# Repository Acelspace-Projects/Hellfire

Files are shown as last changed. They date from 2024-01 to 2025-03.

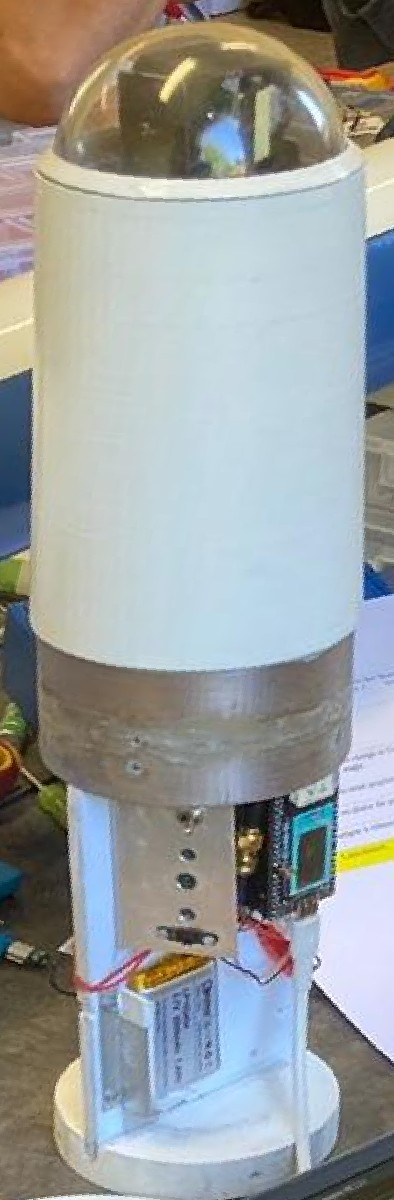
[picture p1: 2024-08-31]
Documentation/RapportDeProjet/img/IMG-20240712-WA0011~2.jpg

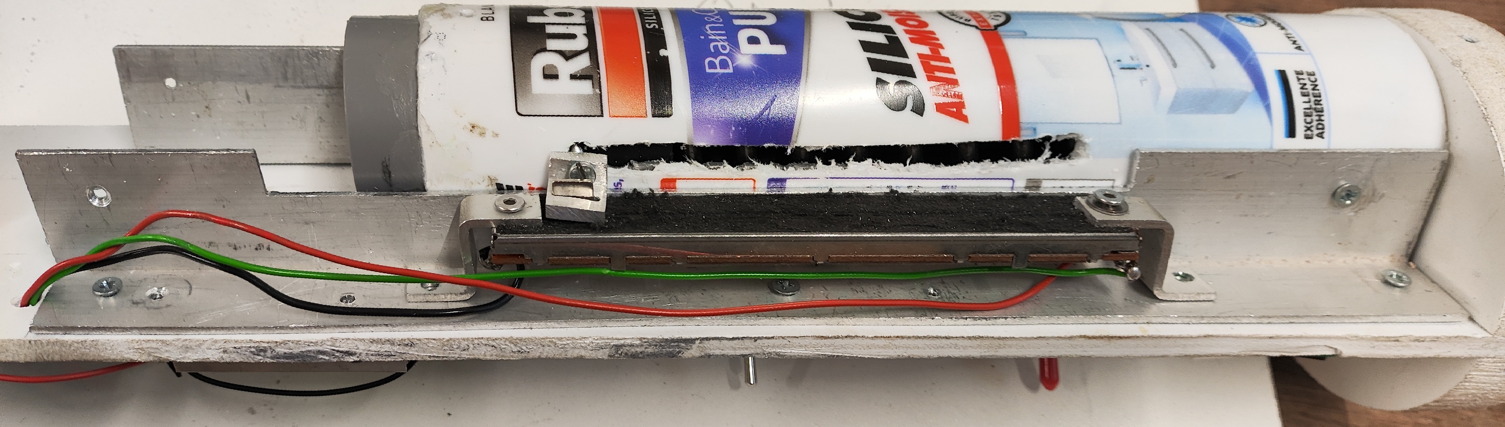
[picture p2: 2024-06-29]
Documentation/RapportDeProjet/img/IMG_20240511_170722~2.jpg

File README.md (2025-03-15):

<h1 align="center">
    <br>
    <a href="https://github.com/Acelspace-Projects/Hellfire">
        Acelspace logo
    </a>
    <br>
    <b>Hellfire</b>
</h3>

<h3 align="center">
    Ceci est un dépot pour le projet Hellfire utilisé pour le versionning et pour avoir des backups.
</h3>

<div class="badges" align="center">
    
    
</div>

---

### Description
Hellfire est un projet du club Acelspace.

### Liens
- [StabTraj](https://github.com/Acelspace-Projects/Hellfire/blob/main/Documentation/StabTraj/ST-(StabTraj)_Hellfire.xlsx)
- [Dossier de définition](https://github.com/Acelspace-Projects/Hellfire/blob/main/Documentation/DossierDeDefinition/DDD_Hellfire.pdf)
- [Dossier technique](https://github.com/Acelspace-Projects/Hellfire/blob/main/Documentation/DossierTechnique/DT_Hellfire.pdf)

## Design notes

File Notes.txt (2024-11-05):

# Matériel final:

## Meca:
* https://www.ressorts-sodemann.fr/13860 (ressort)

## Elec:
* https://heltec.org/project/wireless-tracker/ (telem + GPS)
* https://www.adafruit.com/product/960 (antenna)
* https://www.adafruit.com/product/851 (antenna adapter)
* https://www.adafruit.com/product/2796 (microcontrolleur)
* https://www.adafruit.com/product/4565 (lsm6dsox+lis3mdl sensor)
* https://www.adafruit.com/product/258 (x2 batteries)

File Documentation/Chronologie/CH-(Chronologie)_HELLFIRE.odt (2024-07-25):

Chronologie de Hellfire

H- | Action | Lieu | Matériel | Qui?
Toujours | Lire et porter la chronologie | -- | Chronologie | Dimitri
-- | Rassemblement du matériel | Zone travail club | Chronologie Tournevis+Clé allen Piles/Batteries chargées Jack Dispositif de télémesure Scotch+couteau Ordinateur | Tous
-- | Vérification minuterie principale: la trappe s'ouvre après 16s | Zone travail club | Tournevis | Clément
-- | Récupération matériel | Zone travail club | Voir liste | Tous
-- | Dévissage de l’ogive pour Changement des piles Formatage des cartes SD | Zone travail club | Tournevis, piles, scotch, ordinateur | Clément
2h | Repliage parachute | Zone travail club | Parachute | Tous
1h45 | Verrouillage de la trappe | Zone travail club | Mains | Clément
1h20 | Transport zone tente | Camion militaire | Voir Liste | Tous
45m | Transport zone rampe | Camion militaire | Voir Liste | Tous
42m | Activation de la station sol | Rampe de lancement | Ordinateur, Dispositif de télémesure | Dimitri
40m | Mettre la fusée en rampe | Rampe de lancement | Fusex | Tous
35m | Fixage du fil jack à la rampe Fixage du fil jack à la fusée | Rampe de lancement | Fil jack | Clément
32m | →Allumage du séquenceur principal: - Diode bleue allumée - Diode blanche allumée - Diode rouge allumée ⚠️ Aucune diode ne clignote !! →Activation de l’expérience du tensionomètre: Vérification diode verte allumé →Activation de la télémétrie: Demander autorisation émission 868.138 Mhz Allumage => diode blanche allumée Vérification de la connection à :la station sol La connection GPS est en initialisation →Activation de l'expérience IMU: Dernier interrupteur du panneau principal | Rampe de lancement | Tournevis | Clément
26m | Remettre les vitres de protection des panneaux de contrôle en place + SCOTCH | Rampe de lancement | Mains | Clément
25m | →Allumage caméra : - enlever le dôme, - allumer la caméra - remettre le dôme -> led allumée →Vérification de l'obtention des positions GPS | Rampe de lancement | Mains | Clément
10m | Faire monter la rampe et l'orienter dans le bon angle | Rampe de lancement | Manette de contrôle de la rampe | Gars du CNES
8m | Retour en zone pupitre (lancement) Retour en tente Jupiter (télem) | -- | -- | Clément Dimitri
6m | Mise en place du propulseur | Rampe de lancement | Propulseur | Pyro-techniciens
10s | Compte à rebours | Tente | Voix | Tous
- | Lancement | Pupitre de mise à feu | Mains | Clément

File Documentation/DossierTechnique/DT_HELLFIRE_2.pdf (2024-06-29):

Dossier Technique Hellfire – Hellfire FX10 – 2024-06-09

# DOSSIER TECHNIQUE HELLFIRE

2024

# FAJAL Dimitri CHAUVIN Geoffroy LORIN DE LA GRANDMAISON Clément LORIN DE LA GRANDMAISON Alexandre

Hellfire FX10 – 1/7

# SOMMAIRE

## I. Plan général _________________________ Page 3 II. Conception mécanique ________________ Page 4

1) Informations générales | Page 4
2) Montage ailerons | Page 4
3) Système de retenue du propulseur | Page 4

## III. Système d’éjection _________________ Page 5

1) Plan mécanique | Page 5
2) Plan électrique (séquenceur) | Page 5

## IV. Expériences (TensionomèTRE TRAJECTOGRAPHIE caméra) _________________________________ Page 6

1) Tensionomètre | Page 6
2) TRAJECTOGRAPHIE | Page 7
3) Caméra | Page 7

# I. PLAN GÉNÉRAL

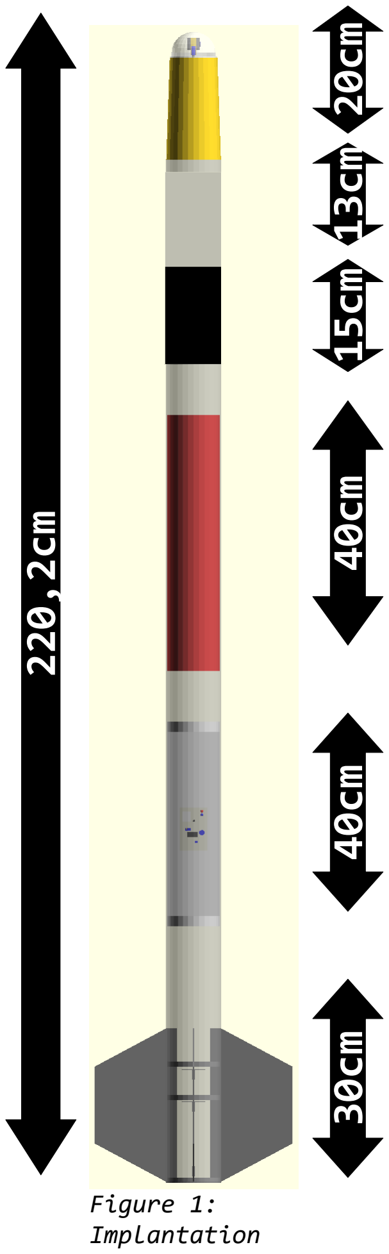
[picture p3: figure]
Xmm; Figure 1: Implantation

→ Ogive dôme sur un rétreint, servomoteur et caméra rotative (180) soutenue par un ventilateur

→ Support secondaire : Télémétrie LoRa et prise de mesures d’accélération et de rotation

→ Centrale inertielle

→ Trappe d’éjection du parachute

→ Support principal contenant l’expérience secondaire de mesure de la tension aux sangles du parachute (tensionomètre), le séquenceur principal et le panneau de contrôle

→ Montage des ailerons et système de retenue du propulseur

Nous utilisons un total de 5 piles 9V : trois dans la minuterie secondaire et deux dans la minuterie principale.

# II. CONCEPTION MÉCANIQUE

# 1) INFORMATIONS GÉNÉRALES

La peau porteuse est un tube en aluminium de 2mm d’épaisseur, de 100mm de diamètre et de 2m de long. Elle offre une grand solidité. L’ensemble des montages à l’intérieur sont solidement
accroché au tube par des vis.

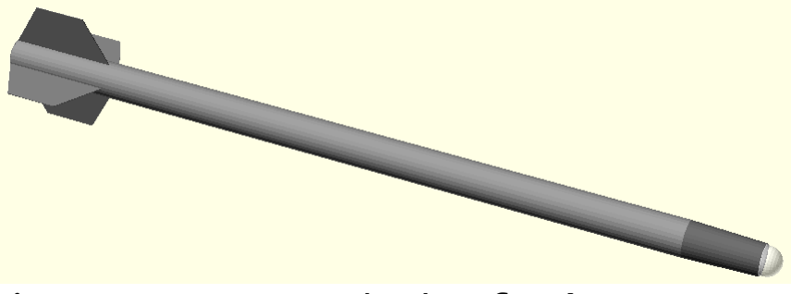
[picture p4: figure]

L’ogive est formée de deux parties : un rétreint réduisant le diamètre à 80mm et un dôme de plastique sur le dessus (ce montage permet l’installation d’une caméra). Le tout mesure 19,5 cm en hauteur.

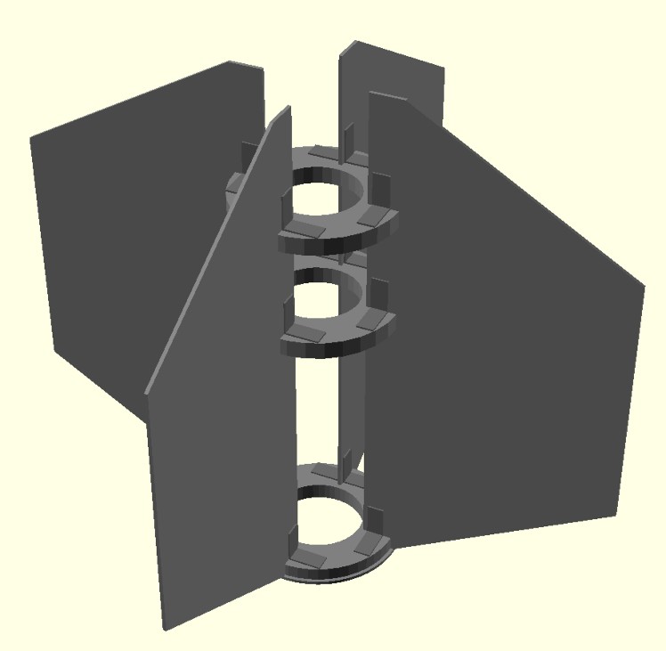
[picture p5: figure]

# 2) MONTAGE AILERONS

Les ailerons sont attachés à trois bagues en aluminium à l’aide d’équerres de métal.
Le montage complet est accroché au tube par avec des vis. La bague la plus inférieure est la plaque de poussée.
Elle transfère la poussée du propulseur au corps de la
fusée.

# 3) SYSTÈME DE RETENUE DU PROPULSEUR

Le propulseur est retenu par un petit montage en métal
accroché à la plaque de poussée.
Celui-ci est construit à l’aide d’un « Sandwich » de pièces en aluminiums usinées.
Pour monter le propulseur, il suffit de l’insérer dans le corps de la fusée. Lorsqu’il est bien montée, un petit « clic » est audible lorsque la pêne ressort du montage.
Pour enlever le propulseur, il faut pousser la poignée avec le doigt. Étant accroché à la pêne il relâchera le propulseur qui peut alors être retiré.

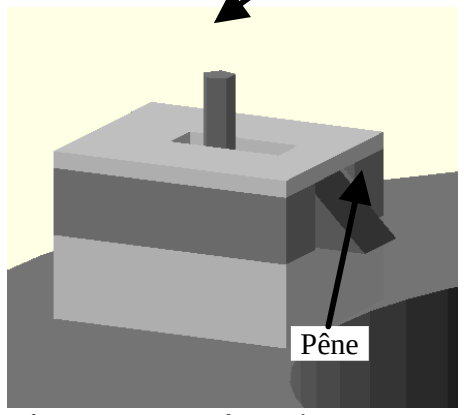
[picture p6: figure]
Pêne

Figure 4: Sytème de retenue du propulseur

Poignée

Figure 3: Montage des
ailerons

Figure 2: Corps de la fusée

# III. SYSTÈME D’ÉJECTION

# 1) PLAN MÉCANIQUE

Le système de récupération est un parachute de ballon sonde circulaire éjecté latéralement de la fusée. Pour cela, il est attaché à la trappe qui l’emporte lors de son ouverture. Afin de s’assurer de l’ouverture de la

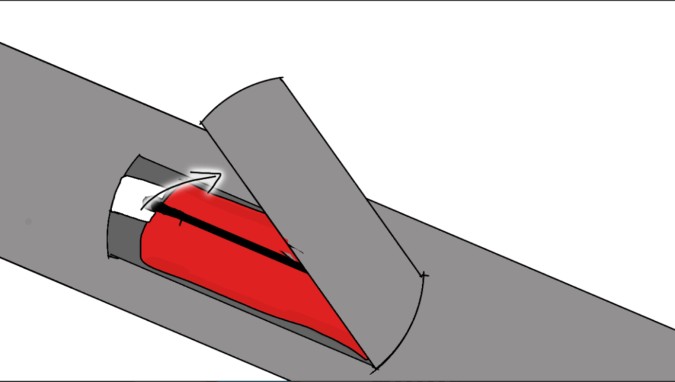
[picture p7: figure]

trappe, elle est poussée par une lame d’essuie-glace à la manière d’un ressort.

# 2) PLAN ÉLECTRIQUE (SÉQUENCEUR)

Une minuterie analogique soudée par nos soins permet le décompte de l’ouverture de la trappe. Un peu avant

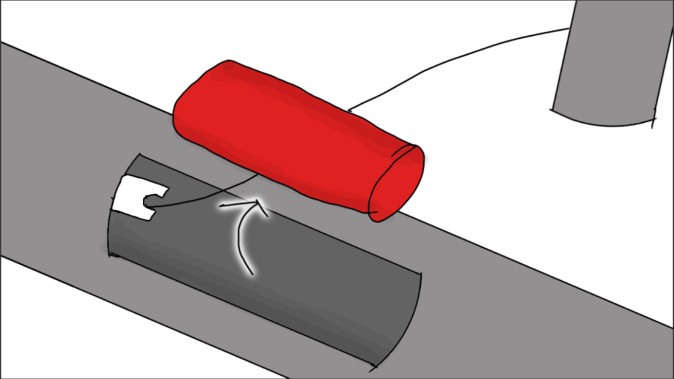
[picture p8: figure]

l’apogée, le séquenceur enclenche un moteur. Sur celui-ci est accroché une cloche qui en tournant libère la trappe.

Figure 5: Ejection de la
trappe

Figure 6: Sortie du
parachute

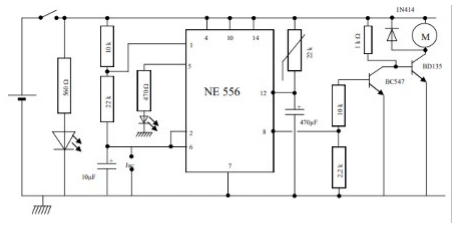
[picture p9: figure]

Figure 7: Schéma électronique du

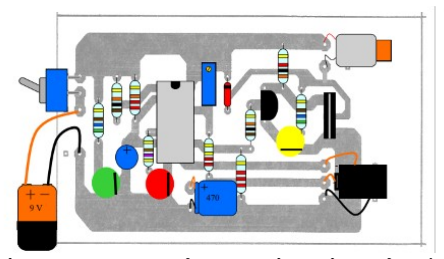
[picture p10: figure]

séquenceur | Figure 8: Représentation imagée du séquenceur

# IV. EXPÉRIENCES (TENSIONOMÈTRE TRAJECTOGRAPHIE CAMÉRA)

# 1) TENSIONOMÈTRE

La tension sera mesurée sur les sangles du parachute. Deux ressorts de 15cm chacun sont compressés par de la sortie du parachute. Ainsi le potentiomètre linéaire relié à un Arduino permettent d’effectuer l’acquisition des données qui sont sauvegardées en temps réel sur carte microSD.

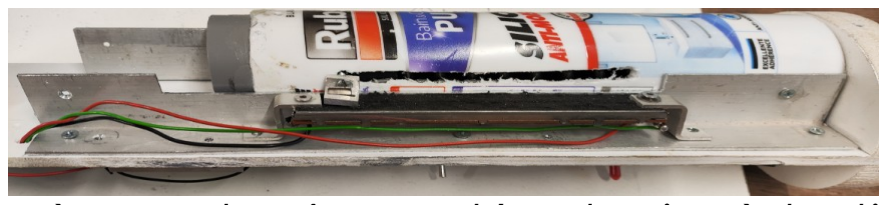
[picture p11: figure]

Après vol, les données sont récupérées et passées au travers d’une fonction de conversion qui transforme les données brutes (de 0 à 1023 données par la carte arduino) en donées exploitables (force exercée en kg).
Cette fonction de conversion est déterminée en appliquant des masses connues (poids d’altère et autres) au système entièrement assemblé. Une courbe d’étalonnage est alors établie sur un tableur pour ensuite faire apparaître la courbe de tendance dont l’équation est la fonction de conversion.

Figure 9: Le système est le même que l'an dernier à la différence qu'il sera maintenant composé de deux ressorts pour une plus grande résistance (1000 N) et qu'il n'est plus aligné avec la sangle (il faut maintenant une poulie dans la trappe)

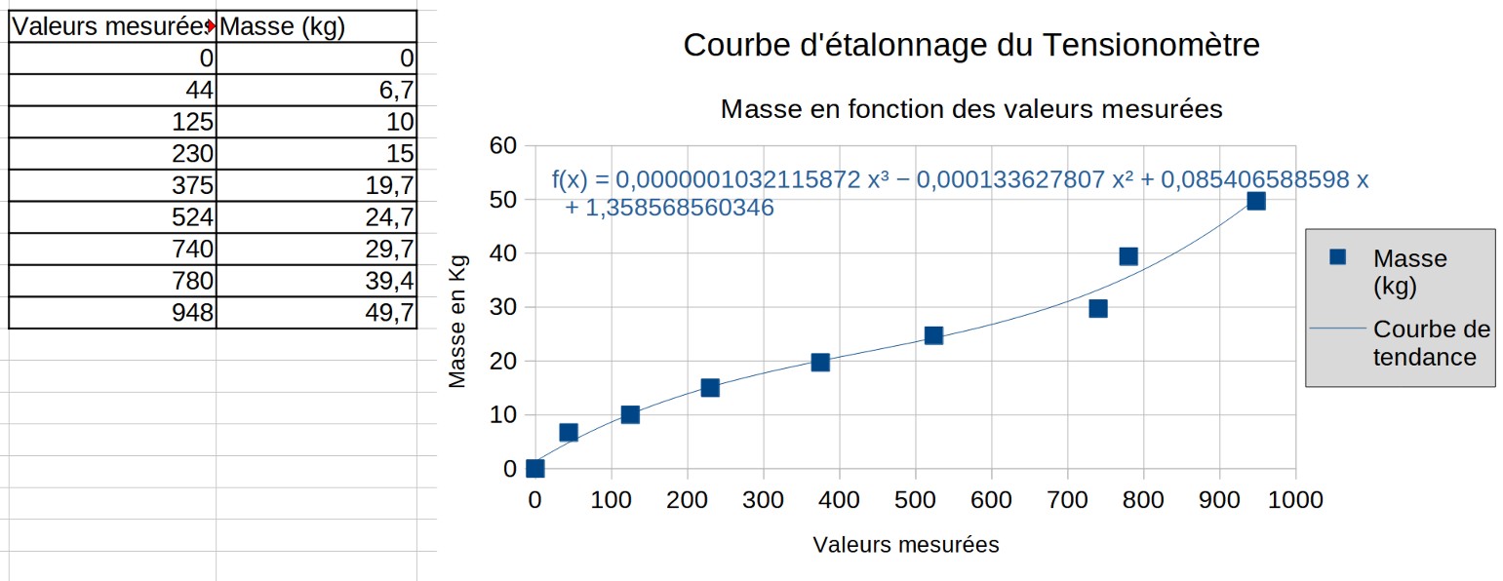
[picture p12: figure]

Figure 10: Courbe d'étalonnage du tensionomètre

# 2) TRAJECTOGRAPHIE

La trajectographie est assurée par de multiples IMUs, capteurs d’accélération et gyroscopes. Ceux que nous utilisons sont les LSM6DSOX (16g) et un LSM6DSO32 (32g). Ces capteurs permettrons d’effectuer post-vol une trajectographie. Un filtre de Kalman sera utilisé.
Le vol a en fait été simulé au préalable par un programme python nous donnant une idée générale du vol de la fusée. Les données accumulées en vol seront retransmises par télémétrie LoRa à l’équipe au sol en temps réel et les données GPS nous permettront de voir la position de la fusée.

# 3) CAMÉRA

Une caméra cubique, de 3.1 cm de côté, se trouve au sommet de la fusée, protégée par un dôme de plexiglas. Les images seront enregistrées sur une carte microSD et pourront être récupérées après le vol. Un système de servomoteur, faisant des allers-retours entre 0° et 180°, permet de l’orienter.
Ayant remarqué une perte de performance de la caméra lorsqu’elle surchauffait, nous avons décidé d’installer un ventilateur dans le dôme.

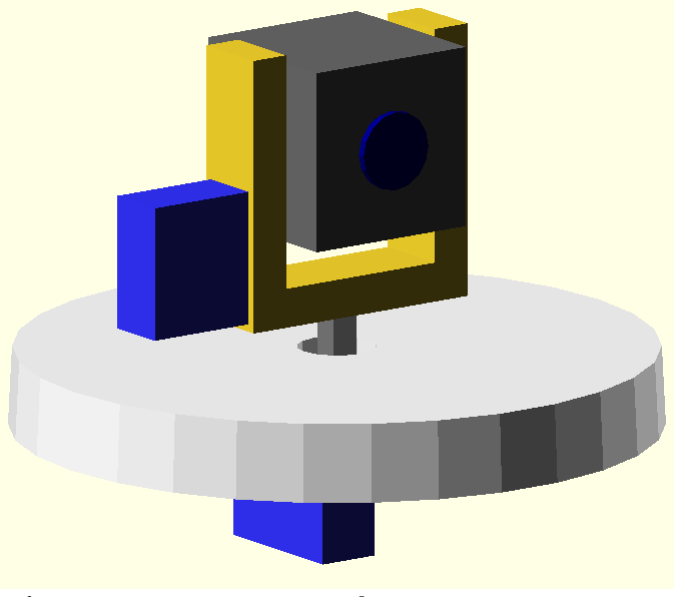
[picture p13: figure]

Figure 11: La caméra

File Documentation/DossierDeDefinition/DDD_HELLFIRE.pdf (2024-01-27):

Dossier de définition – Hellfire – 2023-2024

# DOSSIER DE DÉFINITION HELLFIRE

2023-2024

# BENAY Clément CHAUVIN Geoffroy FAJAL Dimitri KAE-NUNE Damien LORIN DE LA GRANDMAISON Alexandre LORIN DE LA GRANDMAISON Clément PINGLIER Etienne

Hellfire – 1/12

# SOMMAIRE

## Présentation de l’équipe ________________ Page 3

Présentation générale | Page 3
Les membres de l’équipe | Page 3

## Présentation de KARLAVAGNEN _____________ Page 5 Présentation d’HELLFIRE _________________ Page 6

Objectifs | Page 6
Reprise du corps de KARLAVAGNEN | Page 6

## Expériences _____________________________ Page 9

Mesures de la tension exercée sur les sangles du parachute «le
tensionomètre» | Page 9
Caméra montée sur axe rotatif + ventilateur | Page 10
Mesures de la vitesse (Pitot, Venturi et accéléromètre) | Page 11
Mesures de l’altitude et de la température | Page 12

# PRÉSENTATION DE L’ÉQUIPE

# PRÉSENTATION GÉNÉRALE

Notre groupe est constitué de 6 étudiants aux études variées (médecine, commerce, prépas) et d’un lycéen (lycée Sonia Delaunay à Villepreux). C’est cette diversité qui crée la richesse d’innovation de nos projets. Nous avons déjà mené plusieurs projets auparavant dont 2 projet Fusex ensemble : OGMA et KARLAVAGNEN. Chaque membre a mené à bien plusieurs projets et a donc de l’expérience en terme de conception, d’électronique, de mécanique ou même en programmation. Nous sommes encadrés par Roger POISSON, vétéran du C’SPACE et habitué des projets fusées et Sylvain BEAU, ingénieur en aérospatiale dans les systèmes embarqués.

# LES MEMBRES DE L’ÉQUIPE

Geoffroy CHAUVIN : étudiant à l’ESTACA. 7 projets à son actif dont 2 projets Fusex, OGMA et KARLAVAGNEN.

### Clément LORIN DE LA GRANDMAISON : élève de Première au lycée Sonia

Delaunay à Villepreux. 5 projets à son actif dont un projet Fusex, KARLAVAGNEN. Clément BENAY : étudiant en BTS maintenance des véhicules. 5 projets à son actif dont 2 projets Fusex, OGMA et KARLAVAGNEN.
Damien KAE-NUNE : étudiant en mathématiques, informatique, option éco finance à CYTECH. 5 projets à son actif dont 2 projets Fusex, OGMA et KARLAVAGNEN.
Etienne PINGLIER : étudiant à l’INSA de Rouen. 5 projets à son actif dont 2 projets Fusex, OGMA et KARLAVAGNEN.

### Alexandre LORIN DE LA GRANDMAISON : étudiant en médecine à la

Sorbonne. 5 projets à son actif dont 2 projets Fusex, OGMA et KARLAVAGNEN.

Dimitri FAJAL : étudiant en CPGE MPSI au lycée Jeanne d’Albret. 5 projets à son actif dont 2 projets Fusex, OGMA et KARLAVAGNEN. Chef de projet de la Fusex KARLAVAGNEN l’an passé.
Le chef de projet pour le projet de cette année est Alexandre LORIN DE LA GRANDMAISON.
Illustration | 1 | : Fusex KARLAVAGNEN en rampe

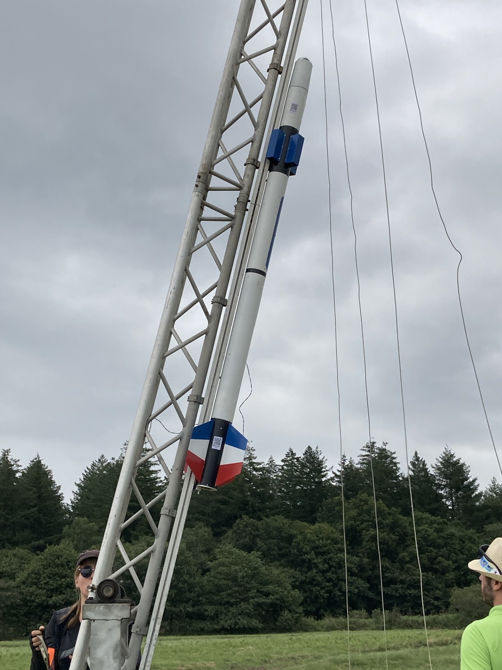
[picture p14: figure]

# PRÉSENTATION DE KARLAVAGNEN

KARLAVAGNEN est le projet que nous avons mis en œuvre durant la campagne de lancement 2022-2023 et qui a abouti à un vol nominal.
Le but du projet était de mesurer la tension aux sangles du parachute via notre tensionomètre maison. Nous mesurions aussi la vitesse de deux manières différentes, par tube de Pitot et par effet Venturi. Pour cela nous avions mis en place 4 blocs de PLA (deux qui contenaient nos capteurs et deux factices pour équilibrer) qui faisaient office d’ailerons : la Fusex possédait donc un bi-empennage pour le moins spécial. A cela s’ajoutait des mesures d’altitude via un BMP 180 et une ogive dôme qui abritait notre caméra montée sur servomoteur et refroidie par un ventilateur dont l’objectif était de filmer l’entièreté du vol. Enfin, notre Fusex embarquait à son bord une carte CATS qui nous fournissait des données en temps réel (position GPS, vitesse, altitude) via de la télémesure (système LoRa, 2,4GHz). Cette carte nous avait été prêté par l’école d’ingénieur Air Esia. Notre Fusex servait de test pour calibrer cette carte afin que nous fassions remonter, post-vol, à Air Esia les différents problèmes que nous aurions pu rencontrer avec la carte. En effet, Air Esia compte utiliser cette carte comme système de backup dans leur Fusex lors du concours européen EuRoc. Ce fut un excellent partenariat qui s’est soldé par une réussite puisque la carte a très bien fonctionné même si nous avons dû leur faire remonter quelques petits problèmes auxquels ils devront faire attention. Fort heureusement, ces problèmes se résolvent par un meilleur réglage de la carte.
Illustration | 2 | : L’équipe Fusex KARLAVAGNEN au complet

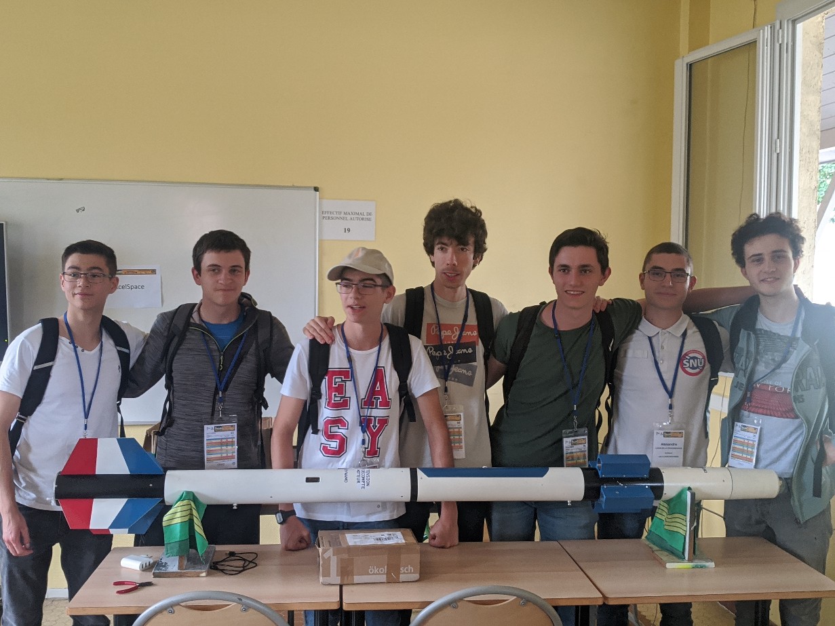
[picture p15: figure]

# PRÉSENTATION D’HELLFIRE

# OBJECTIFS

HELLFIRE est le nouveau projet Fusex que nous allons mettre en œuvre cette année. Il s’agit d’un projet spécial. En effet, nous allons réutiliser le corps de notre ancienne Fusex KARLAVAGNEN qui est intacte suite à un vol nominal. Les objectifs seront les mêmes que ceux de KARLAVAGNEN, à savoir :

- la mesure de la tension aux sangles du parachute via notre tensionomètre maison que nous comptons améliorer.
- la mesure de la vitesse de la Fusex par effet Venturi et par tube de Pitot grâce à quatre blocs de PLA qui contiennent nos capteurs et font office d’ailerons du haut, procurant à la Fusex un bi-empennage d’exception. Cependant, cette année, nous rajoutons un accéléromètre pour avoir encore plus de valeurs à comparer et pouvoir décider lequel des deux systèmes (Pitot ou Venturi) est le plus précis.
- la mesure de l’altitude à laquelle nous rajoutons cette année une mesure de la température grâce un BMP 180.
- filmer le vol grâce à une caméra positionnée dans notre ogive dôme, sur un servomoteur, lui permettant d’avoir une vision 180°. Elle est refroidie par un ventilateur.

# REPRISE DU CORPS DE KARLAVAGNEN

Pour la 1ère fois de l’histoire de notre club, nous comptons relancer une fusex ayant déjà volé. Ce sera donc le corps de Karlavagnen qui va reprendre sa route vers le ciel sous le nom d’Hellfire. Cela est possible pour plusieurs raisons :

- grâce à un vol nominal et une descente sans encombre, Karlavagnen nous est revenue en parfait état. On pourrait même croire qu’elle n’a pas encore volé…
- plusieurs expériences n’ayant pas fonctionné de manière optimale, il serait intéressant pour nous de les améliorer afin que cette fois-ci nous obtenions toutes les données voulues (Tensionomètre et effet Venturi) ;
- la majorité de l’équipe de Karlavagnen étant maintenant en études supérieures, nous ne pouvons que consacrer peu de temps à la réalisation d’une fusex. Avoir toute la mécanique déjà faite nous permet de nous centrer sur ce qui est important, à savoir, les expériences.

Ainsi, l’extérieur sera le même, c’est l’intérieur qui va se faire une peau neuve : toute l’électronique sera vérifié et refaite dans la majorité des cas par précaution. Les expériences seront similaires à celles de Karlavagnen mais seront toutes modifiées de façon à fonctionner de manière optimale. De plus, plusieurs capteurs seront rajoutées. De même, la peinture aura le droit à un petit retouchage.

Illustration | 3 | : Karlavagnen avant le vol | Illustration | 4 | : Karlavagnen après le vol

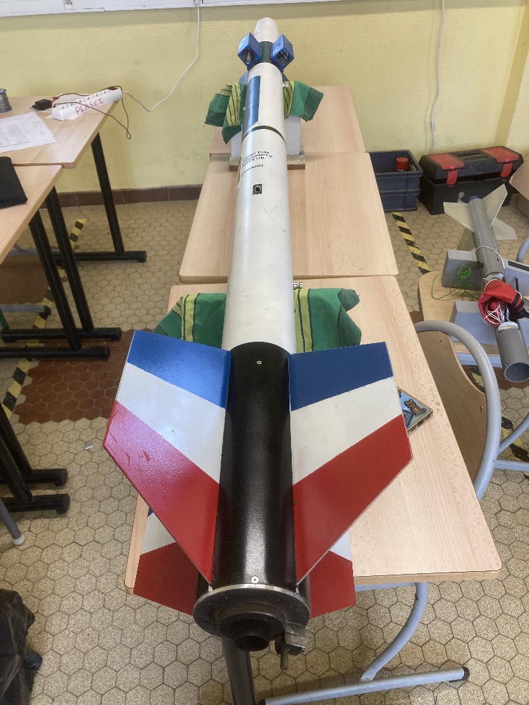
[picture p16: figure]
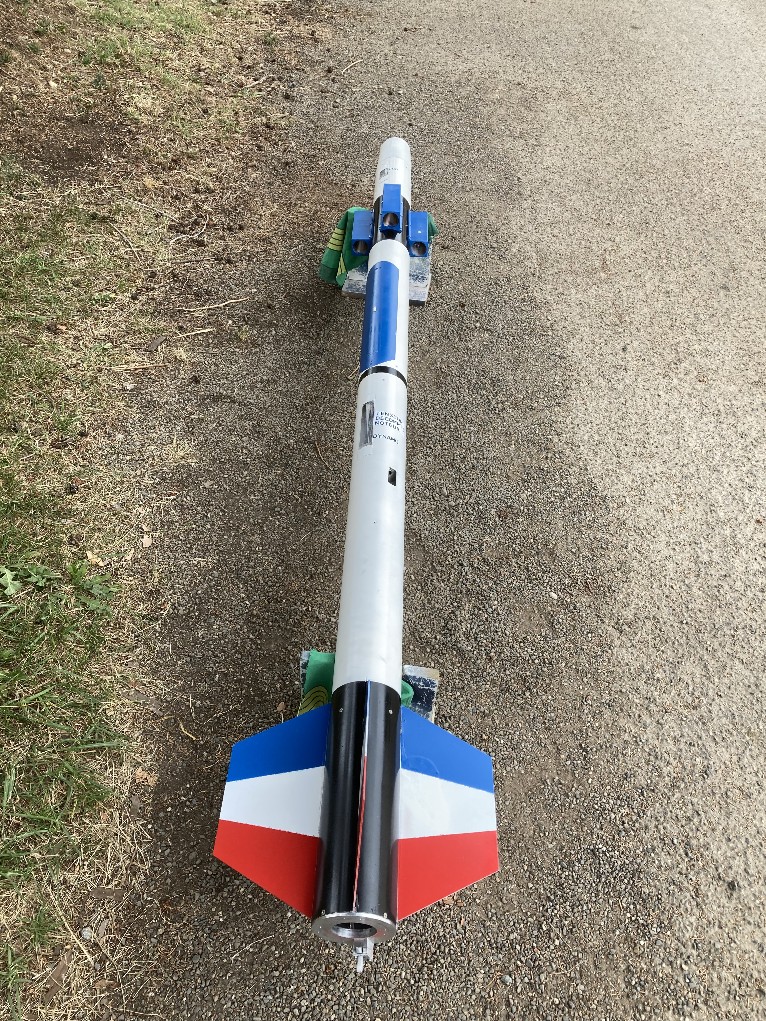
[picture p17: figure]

| | | | | De petites imperfections sont visibles sur la peinture suite au vol mais c’est tout, la mécanique, elle, dans son entièreté, est intacte.

Illustration | 5 | : CAO d’Hellfire

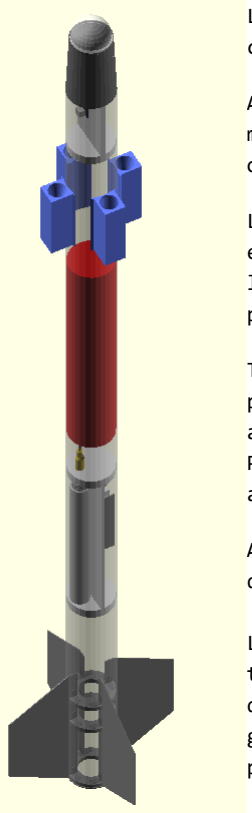
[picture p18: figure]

La partie mécanique d’Hellfire sera donc similaire à celle de Karlavagnen.

Actuellement, nous avons vérifié et testé toute la mécanique ayant volé (ailerons, tube, blocs de PLA, ogive) à la recherche d’éventuelles défaillances.

La seule partie mécanique présentant un léger défaut est un des quatre ailerons qui présente une très
légère | torsion | d’environ | 2° | à | son | extrémité,
probablement due à l’atterrissage. Cela sera corrigé.

Tout le reste est intacte, que ce soit : la bague de poussée, les bagues de centrage propulseur, les 3 autres ailerons, l’ogive, le dôme, les 4 blocs en PLA, la trappe et bien sûr la peau porteuse en aluminium.

Aucune déformation du tube d’aluminium n’a été détectée.

Le principal avantage que nous procure l’usage d’un tube d’aluminium est la grande résistance de ce dernier envers les chocs. C’est d’ailleurs une des garanties nous poussant à relancer cette peau porteuse sans risque.

# EXPÉRIENCES

# MESURES DE LA TENSION EXERCÉE SUR LES SANGLES DU PARACHUTE «LE TENSIONOMÈTRE»

Malheureusement, lors du vol de Karlavagnen, nous sommes à nouveau arrivés en buté du ressort. Cette année, nous comptons refaire entièrement la partie mécanique de cette expérience, en changeant notamment le ressort, pour la faire fonctionner correctement.

La tension sera mesurée sur les sangles du parachute. Toutefois, lors de l’ouverture du parachute, les sangles de ce dernier ne seront pas directement alignées avec le potentiomètre. Elles passeront dans une poulie fixée à l’intérieur de la fusée afin de rediriger l’effort directement sur le potentiomètre. Sans cette poulie, le parachute arracherait le système et la fusée n’aurait alors plus de système de récupération.

Le potentiomètre linéaire sera relié à un Arduino permettant d’effectuer l’acquisition des données qui seront sauvegardées en temps réel sur carte MicroSD.

Le nouveau ressort aura donc une capacité de compression strictement supérieure à 1000N pour nous éviter tout désagrément et nous permettre d’avoir une plage de mesure complète.

Il sera protégé par un tube en PVC qui lui permettra de se compresser de manière linéaire sans déviation. Le tube en PVC sera lui-même immobilisé par deux équerres métalliques présentes de chaque côté. Une encoche présente dans la longueur du tube permettra le raccordement du capteur au ressort. Le capteur pourra donc suivre l’entière compression du ressort pour des mesures les plus précises possibles.

Illustration | 6 | : Le tensionomètre maison qui sera refait en terme de mécanique

# CAMÉRA MONTÉE SUR AXE ROTATIF + VENTILATEUR

Une caméra cubique, de 3.1 cm de côté, se

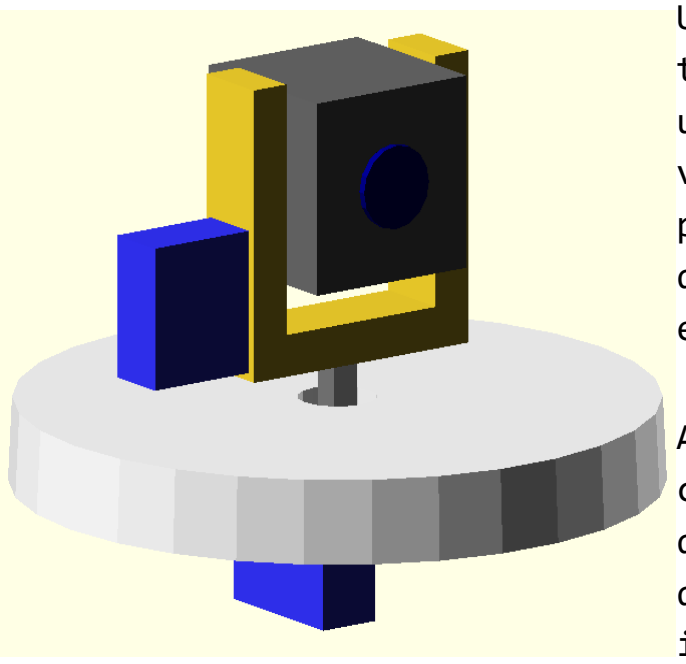
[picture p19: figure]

trouvera au sommet de la fusée, protégée par un dôme de plexiglas. Une vidéo complète du vol sera enregistrée sur une carte MicroSD et pourra être récupérée après le vol. Un système de servomoteur, faisant des allers-retours entre 0° et 180°, permettra de l’orienter.

Ayant remarqué une perte de performance de la caméra lorsqu’elle surchauffait, nous avons décidé d’installer sous elle un ventilateur dans le dôme afin d’éviter d’avoir une vidéo inexploitable.

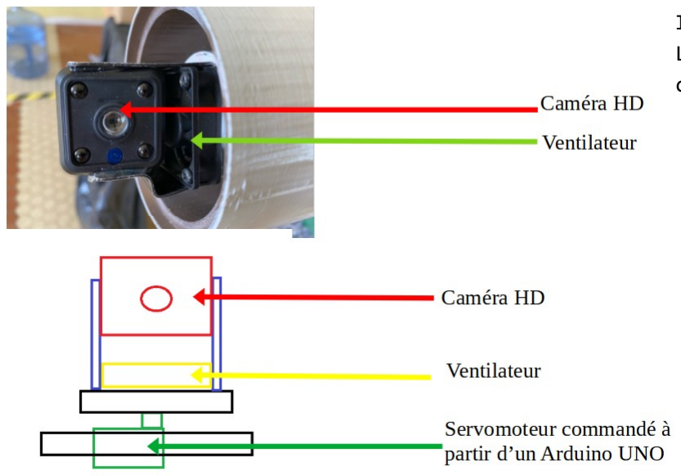
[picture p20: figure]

Illustration | 8 | :
L’ensemble du système
caméra mis en place

Si nous jugeons la qualité de la caméra trop faible quant à la résolution vidéo et au framerate, il se peut que nous la changions.

Illustration | 7 | : La caméra

# MESURES DE LA VITESSE (PITOT, VENTURI ET ACCÉLÉROMÈTRE)

La mesure de la vitesse sur notre fusée va

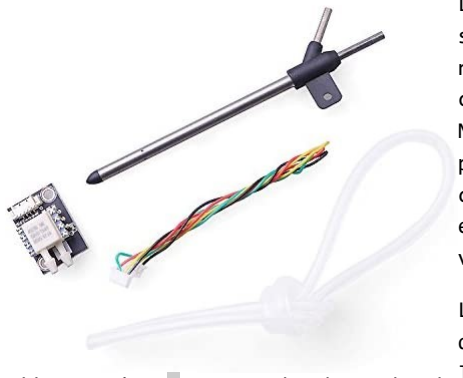
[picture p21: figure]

s’effectuer de deux manières. Tout d’abord nous utiliserons un tube de Pitot (ci-contre) pour réaliser une première mesure. Nous utiliserons ensuite un effet Venturi pour réaliser une seconde mesure que nous comparerons à la première afin d’avoir une estimation beaucoup plus précise de la vitesse de la fusée.

Les données seront récupérées à l’aide de quatre parallélépipèdes en PLA placés sur le haut de la fusée, alignés avec les ailerons dans son axe. Ce système sera le même que celui de notre ancienne Fusex KARLAVAGNEN : deux des 4 blocs en PLA contiendront les tubes de mesure de vitesse, qui achemineront l’air jusqu’au MPX5010DP, capteur différentiel de pression placé sur la carte Arduino.

Ainsi, l’un des blocs contiendra un tube de Pitot et un autre nous permettra d’utiliser l’effet Venturi avec un rétrécissement du diamètre intérieur. Les deux autres seront factices, afin d’éviter de perturber la stabilité.

Illustration | 9 | : Exemple de tube de
Pitot (à titre illustratif)

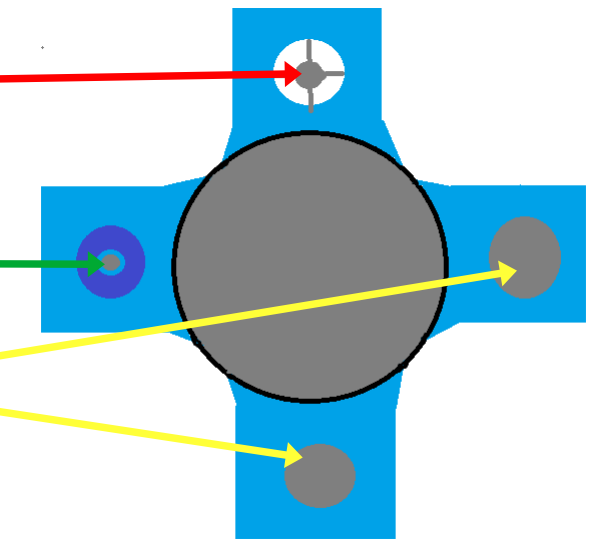
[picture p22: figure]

Tube de pitot

Tube Venturi

Illustration | 10 | : Positionnement des
différentes expériences (Venturi et Pitot)

Tubes factices qui
permettent
d’équilibrer la fusée

Pour avoir encore plus de précision quant à la fiabilité des mesures, nous avons décidé d’intégré en complément de ces dernières, un accéléromètre, géré par un Arduino NANO, qui nous permettra post-vol de déterminer lequel des deux système (Pitot ou Venturi) est le plus fiable.
Enfin, il faut savoir que cette année nous allons améliorer la fixation du tube de Pitot en rajoutant un tube de centrage métallique à l’intérieur du bloc de PLA. Sur la Fusex Karlavagnen, nous avions eu beaucoup d’interférences dues aux vibrations du tube Pitot. En fixant mieux Pitot, nous comptons régler ce problème. Du côté de Venturi aucun changement à venir si ce n’est que nous ne nous tromperons pas quant au raccordement du capteur à la basse et haute pression. En effet, lors du vol de Karlavagnen, les raccordements étaient inversés ce qui nous avait empêché d’obtenir des mesures exploitables.

# MESURES DE L’ALTITUDE ET DE LA TEMPÉRATURE

L’Arduino qui s’occupera des mesures du tensionomètre gérera aussi un BMP 180 qui nous fournira des mesures d’altitude que nous pourrons ensuite comparer avec le Stabtraj. Les données seront enregistrées sur carte MicroSD et exploitables à la fin du vol. Ce même BMP 180 mesurera aussi la température de la fusée durant toute la durée du vol.

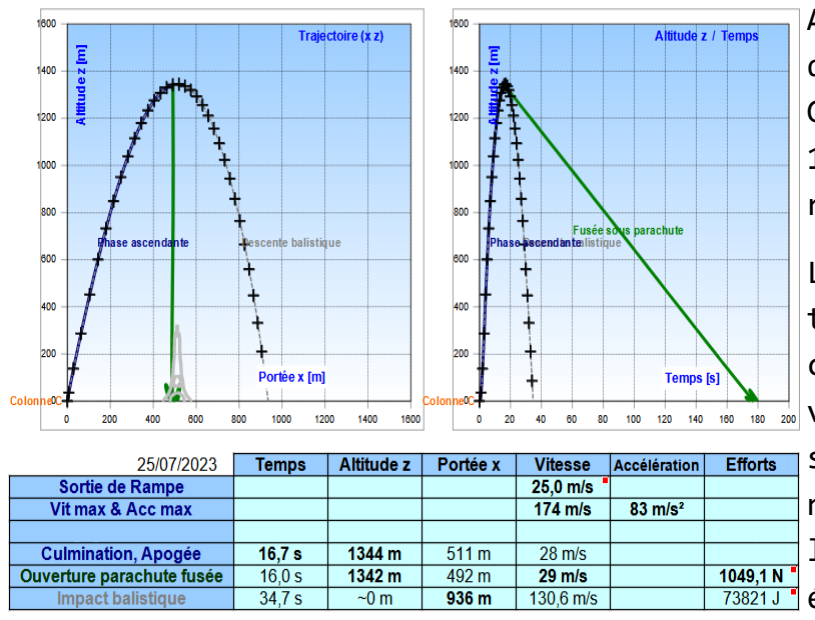
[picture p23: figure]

Avec un Cx de 0,6 le Stabtraj nous donne une altitude maximum de 1344m. Grâce aux mesures que prendra le BMP
180, | nous | comptons | comparer | la
réalité à la simulation.
Le BMP 180 pouvant aussi mesurer la température, nous comptons utiliser cette fonction afin d’étudier les variations de température qu’aura subi notre tube en aluminium. Cela nous permettra de savoir post-vol si les composants électroniques auront été mis à rude épreuve ou pas.
Illustration | 11 | : Stabtraj d’HELLFIRE

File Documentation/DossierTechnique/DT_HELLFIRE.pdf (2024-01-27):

DOSSIER TECHNIQUE HELLFIRE | – | HELLFIRE | FX | – | 2023/2024

# DOSSIER TECHNIQUE HELLFIRE

2023/2024

# FAJAL Dimitri CHAUVIN Geoffroy LORIN DE LA GRANDMAISON Alexandre LORIN DE LA GRANDMAISON Clément BENAY Clément KAE-NUNE Damien PINGLIER Etienne

HELLFIRE | FX | – | 1/15

# SOMMAIRE

## I. Plan général _________________________ Page 3 II. Conception mécanique ________________ Page 4

1) Informations générales | Page 4
2) Montage ailerons | Page 4
3) Système de retenue du propulseur | Page 4
4) Reprise du corps de notre ancienne fusex KARLAVAGNEN ...... Page 5

## III. Système d’éjection _________________ Page 7

1) Plan mécanique | Page 7
2) Plan électrique (séquenceur) | Page 7

## IV. Expériences (Tensionomètre, mesures de

vitesse, accéléromètre, mesures d’altitude,

## mesures de températures et caméra) ______ Page 8

1) Tensionomètre | Page 8
2) Mesures de vitesse + accéléromètre | Page 9
3) Mesures d’altitude + température | Page 10
4) Caméra montée sur servomoteur | Page 11
5) Alimentation des expériences | Page 12
6) Stockage des données | Page 13
7) Étalonnage des expériences | Page 13
HELLFIRE | FX | – | 2/15

# I. PLAN GÉNÉRAL

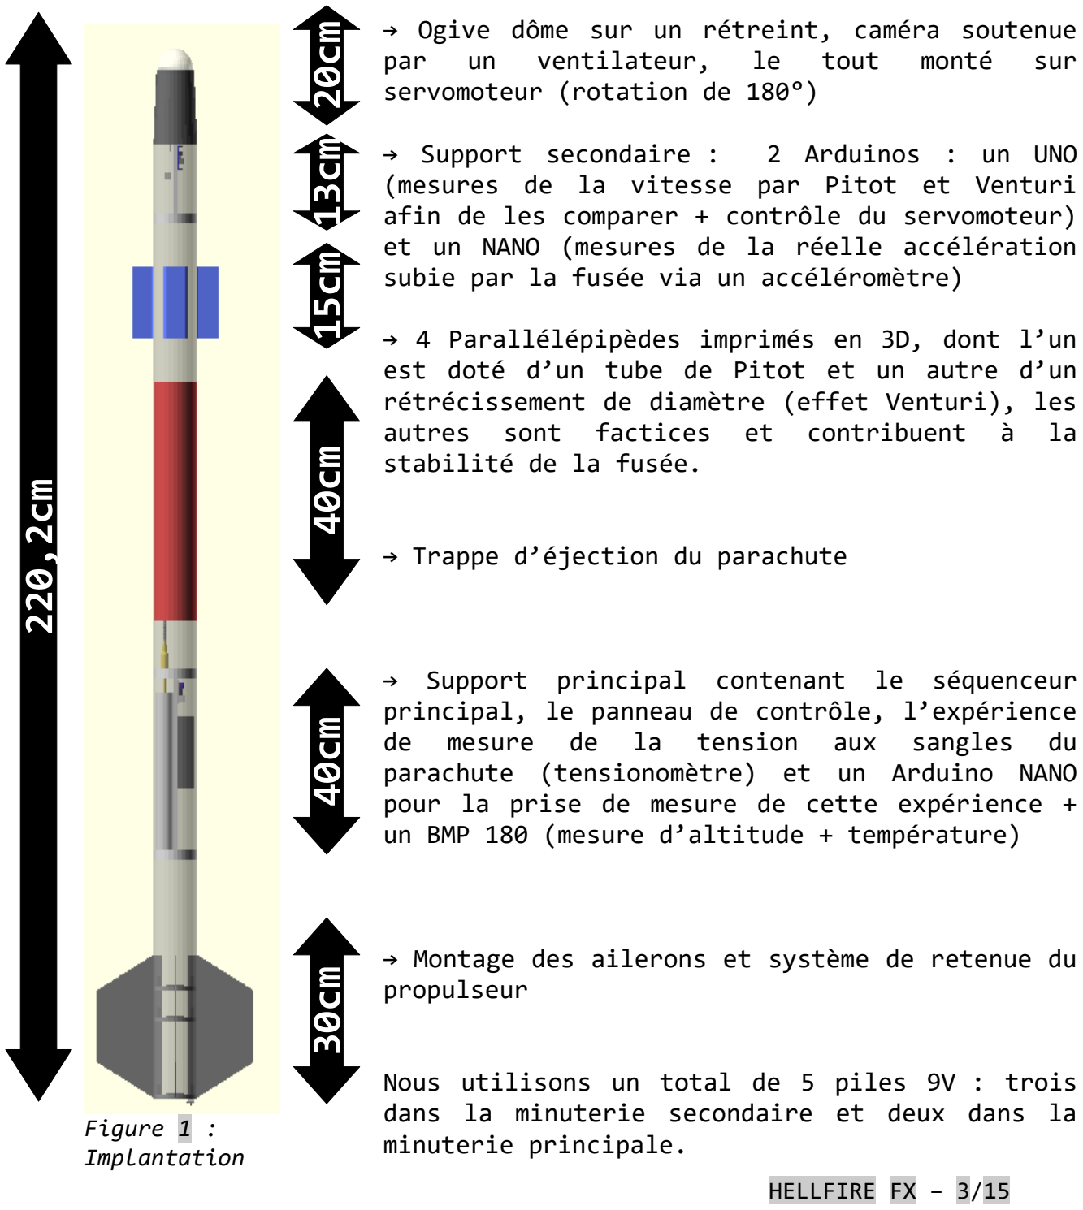
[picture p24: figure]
HELLFIRE; Xmm; Figure; Implantation; par; ventilateur,; tout; monté; sur; servomoteur (rotation de 180°); → Support secondaire :; 2 Arduinos : un UNO; stabilité de la fusée.; → Trappe d’éjection du parachute; de mesure de la tension aux sangles du; propulseur; minuterie principale.

→ Ogive dôme sur un rétreint, caméra soutenue

(mesures de la vitesse par Pitot et Venturi afin de les comparer + contrôle du servomoteur) et un NANO (mesures de la réelle accélération subie par la fusée via un accéléromètre)

→ 4 Parallélépipèdes imprimés en 3D, dont l’un est doté d’un tube de Pitot et un autre d’un rétrécissement de diamètre (effet Venturi), les autres sont factices et contribuent à la

→ Support principal contenant le séquenceur principal, le panneau de contrôle, l’expérience

parachute (tensionomètre) et un Arduino NANO pour la prise de mesure de cette expérience + un BMP 180 (mesure d’altitude + température)

→ Montage des ailerons et système de retenue du

Nous utilisons un total de 5 piles 9V : trois dans la minuterie secondaire et deux dans la

# II. CONCEPTION MÉCANIQUE

# 1) INFORMATIONS GÉNÉRALES

La peau porteuse est un tube en aluminium de 2mm d’épaisseur, de 100mm de diamètre et de 2m de long. Elle offre une grand solidité. L’ensemble des montages à l’intérieur sont solidement
accroché au tube par des vis.
L’ogive est formée de deux parties : un rétreint

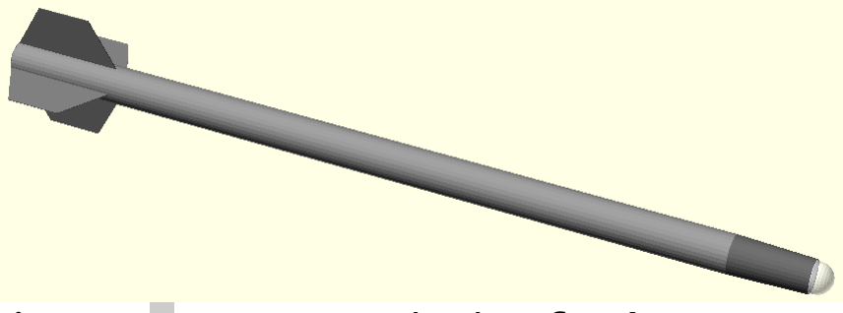
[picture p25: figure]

réduisant le diamètre à 80mm et un dôme de plastique sur le dessus (ce montage permet l’installation d’une caméra). Le tout mesure 19,5 cm en hauteur.

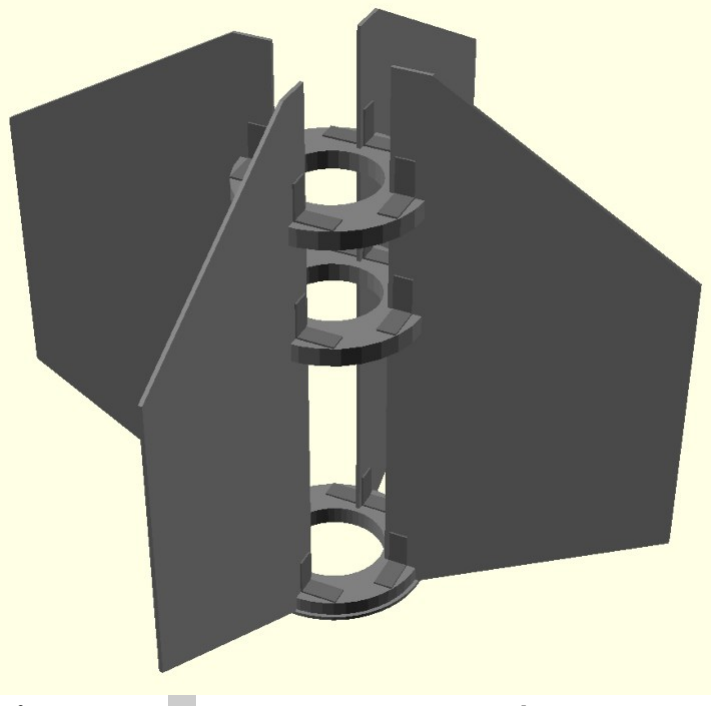
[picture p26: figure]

# 2) MONTAGE AILERONS

Les ailerons sont attachés à trois bagues en aluminium à l’aide d’équerres de métal.
Le montage complet est accroché au tube par avec des vis. La bague la plus inférieure est la plaque de poussée.
Elle transfère la poussée du propulseur au corps de la
fusée.

# 3) SYSTÈME DE RETENUE DU PROPULSEUR

Pêne

Le propulseur est retenu par un petit montage en métal
accroché à la plaque de poussée.
Celui-ci est construit à l’aide d’un «Sandwich» de pièces en aluminiums usinées.
Pour monter le propulseur, il suffit de l’insérer dans le corps de la fusée. Lorsqu’il est bien montée, un petit «clic» est audible lorsque la pêne ressort du montage.
Pour enlever le propulseur, il faut pousser la poignée avec le doigt. Étant accroché à la pêne il relâchera le propulseur qui peut alors être retiré.
HELLFIRE | FX | – | 4/15
Figure | 4 | : Système de
retenue du propulseur

Poignée

Figure | 3 | : Montage des
ailerons
Figure | 2 | : Corps de la fusée

# 4) REPRISE DU CORPS DE NOTRE ANCIENNE FUSEX KARLAVAGNEN

Pour la 1ère fois de l’histoire de notre club, nous comptons relancer une fusex ayant déjà volé. Ce sera donc le corps de Karlavagnen qui va reprendre sa route vers le ciel sous le nom d’Hellfire. Cela est possible pour plusieurs raisons :

- grâce à un vol nominal et une descente sans encombre, Karlavagnen nous est revenue en parfait état. On pourrait même croire qu’elle n’a pas encore volé…
- plusieurs expériences n’ayant pas fonctionné de manière optimale, il serait intéressant pour nous de les améliorer afin que cette fois-ci nous obtenions toutes les données voulues.
- la majorité de l’équipe de Karlavagnen étant maintenant en études supérieures, nous ne pouvons que consacrer peu de temps à la réalisation d’une fusex. Avoir toute la mécanique déjà faite nous permet de nous centrer sur ce qui est important, à savoir, les expériences.

Ainsi, l’extérieur sera le même, c’est l’intérieur qui va se faire une peau neuve : toute l’électronique sera vérifié et refaite dans la majorité des cas par précaution. Les expériences seront similaires à celles de Karlavagnen mais seront toutes modifiées de façon à fonctionner de manière optimale. De plus, plusieurs capteurs seront rajoutées. De même, la peinture aura le droit à un
petit retouchage.

HELLFIRE; sur la peinture suite au vol mais c’est tout, la mécanique, elle, dans son entièreté, est intacte.

Figure | 5 | : Karlavagnen avant le vol | Figure | 6 | : Karlavagnen après le vol De petites imperfections sont visibles

Figure | 7 | : CAO d’Hellfire


La partie mécanique d’Hellfire sera donc similaire à celle de Karlavagnen.

Actuellement, nous avons vérifié et testé toute la mécanique ayant volé (ailerons, tube, blocs de PLA, ogive) à la recherche d’éventuelles défaillances.

La seule partie mécanique présentant un léger défaut est un des quatre ailerons qui présente une très
légère | torsion | d’environ | 2° | à | son | extrémité,
probablement due à l’atterrissage. Cela sera corrigé.

Tout le reste est intacte, que ce soit : la bague de poussée, les bagues de centrage propulseur, les 3 autres ailerons, l’ogive, le dôme, les 4 blocs en PLA, la trappe et bien sûr la peau porteuse en aluminium.

Aucune déformation du tube d’aluminium n’a été détectée.

Le principal avantage que nous procure l’usage d’un tube d’aluminium est la grande résistance de ce dernier envers les chocs. C’est d’ailleurs une des garanties nous poussant à relancer cette peau porteuse sans risque.

HELLFIRE | FX | – | 6/15

# III. SYSTÈME D’ÉJECTION

# 1) PLAN MÉCANIQUE

Le système de récupération est un parachute de ballon sonde circulaire éjecté latéralement de la fusée. Pour cela, il est attaché à la trappe qui l’emporte lors de son ouverture. Afin de s’assurer de l’ouverture de la


trappe, elle est poussée par une lame d’essuie-glace à la manière d’un ressort.


# 2) PLAN ÉLECTRIQUE (SÉQUENCEUR)

Une minuterie analogique soudée par nos soins permet le décompte de l’ouverture de la trappe. Un peu avant l’apogée, le séquenceur enclenche un moteur. Sur celui-ci est accroché une cloche qui, en tournant, libère la trappe.

HELLFIRE | FX | – | 7/15


Figure | 10 | : Schéma du séquenceur
Figure | 8 | : Éjection de
la trappe
Figure | 9 | : Sortie du
parachute

# IV. EXPÉRIENCES (TENSIONOMÈTRE, MESURES

DE VITESSE,

# ACCÉLÉROMÈTRE, MESURES D’ALTITUDE, MESURES DE TEMPÉRATURES ET CAMÉRA)

# 1) TENSIONOMÈTRE

Malheureusement, lors du vol de Karlavagnen, nous sommes à nouveau arrivés en buté du ressort. Cette année, nous refaisons entièrement la partie mécanique de cette expérience, en changeant notamment le ressort, pour la faire fonctionner correctement.

La tension est mesurée sur les sangles du parachute. Toutefois, lors de l’ouverture du parachute, les sangles de ce dernier ne sont pas directement alignées avec le potentiomètre. Elles passent dans une poulie fixée à l’intérieur de la fusée afin de rediriger l’effort directement sur le potentiomètre. Sans cette poulie, le parachute arracherait le système et la fusée n’aurait alors plus de système de récupération.

Le potentiomètre linéaire est relié à un Arduino permettant d’effectuer l’acquisition des données qui sont sauvegardées en temps réel sur carte MicroSD.

Le nouveau ressort aura donc une capacité de compression strictement supérieure à 1000N pour nous éviter tout désagrément et nous permettre d’avoir une plage de mesure complète. Il est protégé par un tube en PVC qui lui permet de se compresser de manière linéaire sans déviation. Le tube en PVC est lui-même

HELLFIRE | FX | – | 8/15

immobilisé par deux équerres métalliques présentes de chaque côté. Une encoche présente dans la longueur du tube permet le raccordement du capteur au ressort. Le capteur peut donc suivre l’entière compression du ressort pour des mesures les plus précises possibles.

# 2) MESURES DE VITESSE + ACCÉLÉROMÈTRE

Nous utilisons deux systèmes de mesures de la vitesse afin de les comparer. Le premier utilise un tube de Pitot et le second exploite l’effet venturi. Les deux systèmes sont montés sur un support en PVC et les données sont compilées grâce à une carte Arduino, puis enregistrées sur carte MicroSD. Pour avoir encore plus de précision quant à la fiabilité des mesures, nous avons décidé d’intégré un accéléromètre, géré par un Arduino NANO, qui nous permettra post-vol de déterminer lequel des deux système (Pitot ou Venturi) est le plus fiable.

De plus, les données sont récupérées à l’aide de quatre parallélépipèdes imprimés en PLA, placés sur le haut de la fusée et alignés avec les ailerons dans son axe. Deux d’entre eux contiennent les tubes de mesure de vitesse, qui acheminent l’air jusqu’au MPX5010DP, capteur différentiel de pression placé sur la carte Arduino.

En effet, l’un des blocs contient un tube de Pitot et un autre nous permet d’utiliser l’effet Venturi avec un rétrécissement du diamètre intérieur. Les deux autres sont factices, afin d’éviter de perturber la stabilité.

Enfin, il faut savoir que cette année nous améliorons la fixation du tube de Pitot en rajoutant un tube de centrage métallique à l’intérieur du bloc. Sur la Fusex Karlavagnen, nous avions eu beaucoup d’interférences dues aux vibrations du tube Pitot. En fixant mieux Pitot, nous comptons régler ce problème. Du côté de Venturi aucun changement à venir si ce n’est que nous ne nous tromperons pas

HELLFIRE | FX | – | 9/15
Figure | 11 | : Le système n'est plus aligné avec la sangle (il faut
maintenant une poulie dans la trappe)

quant au raccordement du capteur à la basse et haute pression. En effet, lors du vol de Karlavagnen, les raccordements étaient inversés ce qui nous avait empêché d’obtenir des mesures exploitables.


# 3) MESURES D’ALTITUDE + TEMPÉRATURE

L’Arduino qui s’occupe des mesures du tensionomètre gère aussi un BMP 180 qui nous fournira des mesures d’altitude que nous pourrons ensuite comparer avec le Stabtraj. Les données seront enregistrées sur carte MicroSD et exploitables à la fin du vol. Ce même BMP 180 mesurera aussi la température de la fusée durant toute la durée du vol.


Avec un Cx de 0,6 le Stabtraj nous donne une altitude maximum de 1344m. Grâce aux mesures que prendra le BMP
180, | nous | comptons | comparer | la
réalité à la simulation.
Le BMP 180 pouvant aussi mesurer la température, nous comptons utiliser cette fonction afin d’étudier les variations de température qu’aura subi notre tube en aluminium. Cela nous permettra de savoir post-vol si les composants électroniques auront été mis à rude épreuve ou pas.
HELLFIRE | FX | – | 10/15
Figure | 13 | :
Bloc contenant
le tube de
Pitot
Figure | 12 | :
Bloc
exploitant
l’effet
Venturi
Figure | 14 | : Stabtraj

# 4) CAMÉRA MONTÉE SUR SERVOMOTEUR


Une caméra cubique, de 3.1 cm de côté, se trouve au sommet de la fusée, protégée par un dôme de plexiglas. Les images seront
enregistrées | sur | une | carte | MicroSD | et
pourront être récupérées après le vol. Un système de servomoteur, faisant des allers-
retours | entre | 0° | et | 180°, | permet | de
l’orienter.
Ayant remarqué une perte de performance de la caméra lorsqu’elle surchauffait, nous
avons | décidé | d’installer | sous | elle | un
ventilateur dans le dôme afin d’éviter d’avoir une vidéo inexploitable.


Figure | 16 | : l’ensemble du
système caméra
HELLFIRE | FX | – | 11/15
Figure | 15 | : La caméra

# 5) ALIMENTATION DES EXPÉRIENCES


Figure | 17 | : schéma de l’alimentation de
l’Arduino UNO
Sa consommation est d’environ 50mAh.


Figure | 18 | : alimentation du ventilateur


Figure | 19 | : alimentation d’un Arduino NANO

La fusex embarque 2 Arduinos NANO de ce type. Les deux alimentations sont similaires.
Un NANO s’occupe du tensionomètre et du BMP 180 (mesures d’altitude et de température).
Un 2ème NANO s’occupe de gérer l’accéléromètre.
Leur consommation est d’environ 20mAh.
HELLFIRE | FX | – | 12/15

# 6) STOCKAGE DES DONNÉES


Figure | 20 | : raccordement du
lecteur MicroSD à l’Arduino UNO

Toutes les données de nos mesures sont stockées sur carte MicroSD et exploitables post-vol. Voulant le moins de perte possible, nous enregistrons toutes nos données en temps réel. Pour avoir un maximum de valeurs et donc pouvoir tracer une courbe qui soit la plus représentative qui soit, nous prenons des mesures toutes les 50ms.
Cette année, nous n’embarquons pas de télémesure.

# 7) ÉTALONNAGE DES EXPÉRIENCES

Pour obtenir les valeurs du tube Pitot et du bloc exploitant l’effet Venturi, nous avons placé les blocs en dehors de la fenêtre de la voiture et nous avons roulé à différentes vitesses constantes afin d’obtenir des valeurs qui sont consignées dans les deux premiers tableaux ci-dessus.

Pour obtenir les valeurs du tensionomètre, nous avons simplement fait suspendre plusieurs poids de différentes masses au bout du ressort.

Figure | 21 | : données tube Pitot
Figure | 22 | : données obtenues par effet
Venturi

HELLFIRE

DOSSIER TECHNIQUE HELLFIRE – HELLFIRE FX – 2023/2024

Figure 23 : données du tensionomètre


Ci-dessous voici les différentes courbes d’étalonnage de nos capteurs :

Courbe d'étalonnage du tube Pitot; Valeurs mesurées Courbe de tendance Colonne C Courbe de tendance; Vitesse en Km/h; valeurs mesurées

HELLFIRE FX – 14/15

f(x) = 2,47386759581881 x − 256,602787456446

f(x) = 0,271925305859627 x + 31,2572440437862

Valeurs mesurées en fonction de la vitesse

DOSSIER TECHNIQUE HELLFIRE – HELLFIRE FX – 2023/2024

Courbe d'étalonnage du Tensionomètre; Masse en fonction des valeurs mesurées; Masse (kg); Courbe de tendance; Valeurs mesurées; asse en Kg; Courbe d'étalonnage de l'effet Venturi; Valeurs mesurées Courbe de tendance Colonne C Courbe de tendance; Vitesse en Km/h

HELLFIRE FX – 15/15

f(x) = 0,0000001032115872 x³ − 0,000133627807 x² + 0,085406588598 x f(x) = 0,675510204081633 x − 2,42346938775511

f(x) = 0,113496932515337 x + 35,6042944785276

Valeurs mesurées en fonction de la vitesse

NB : Toutes les données mentionnées ci-dessus ne sont pas définitives et peuvent être amenées à changer si nous décidons de refaire des mesures d’étalonnage.

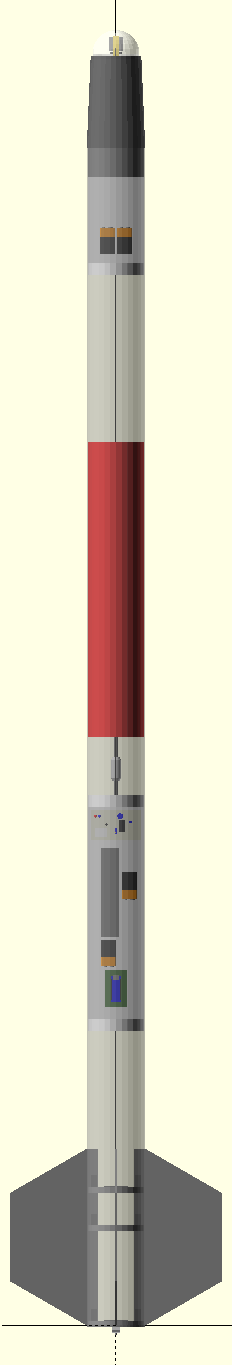
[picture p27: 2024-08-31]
Documentation/RapportDeProjet/img/Hellfire.png

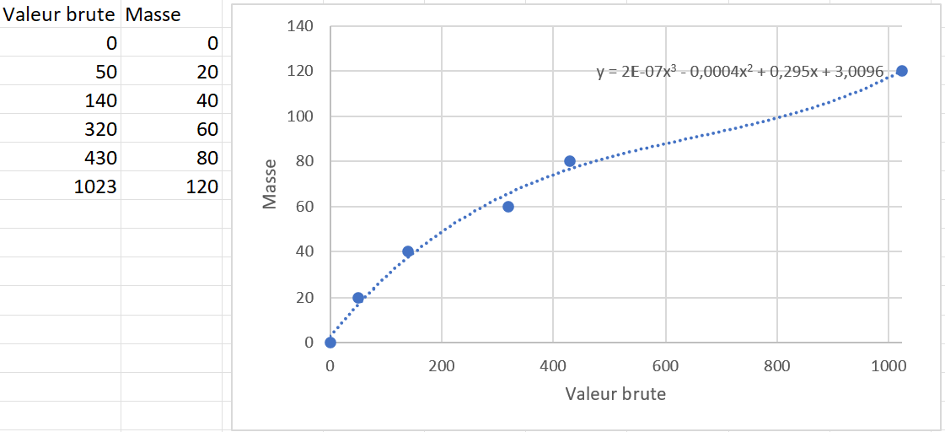
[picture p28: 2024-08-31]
Documentation/RapportDeProjet/img/Capture d'écran 2024-07-30 114446.png

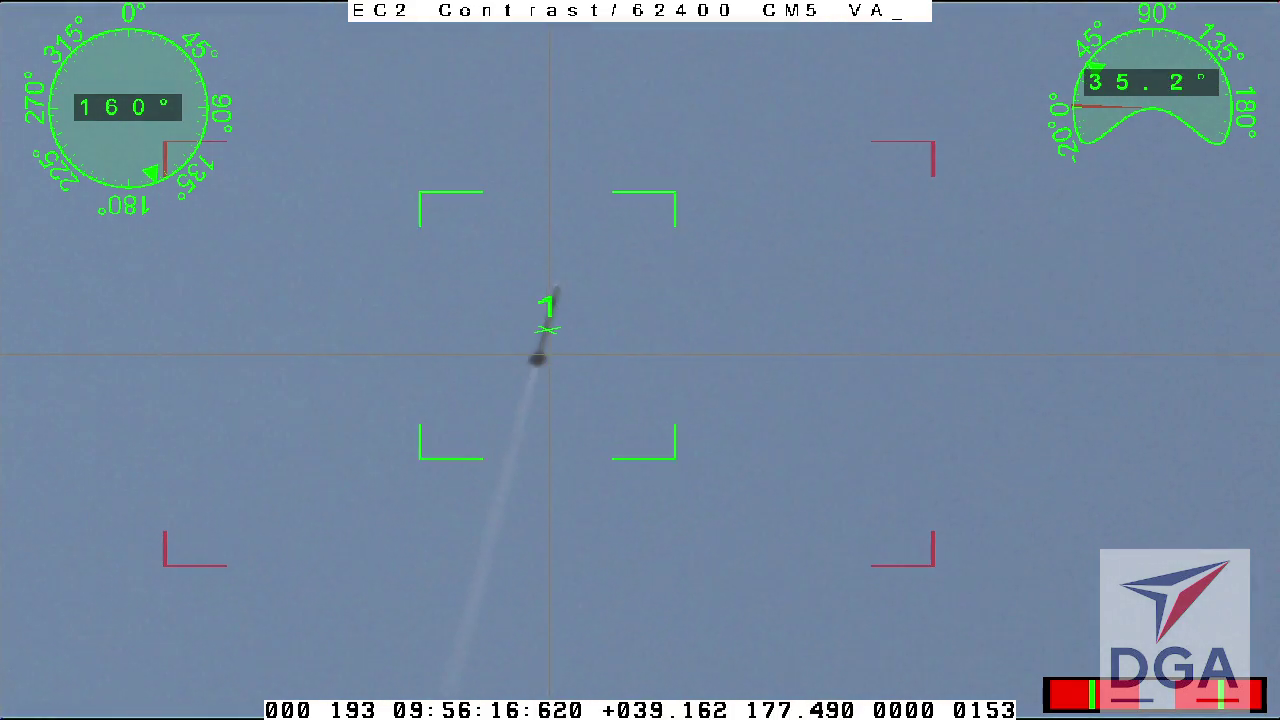
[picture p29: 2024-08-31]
Documentation/RapportDeProjet/img/vlcsnap-2024-07-30-11h55m52s442.png

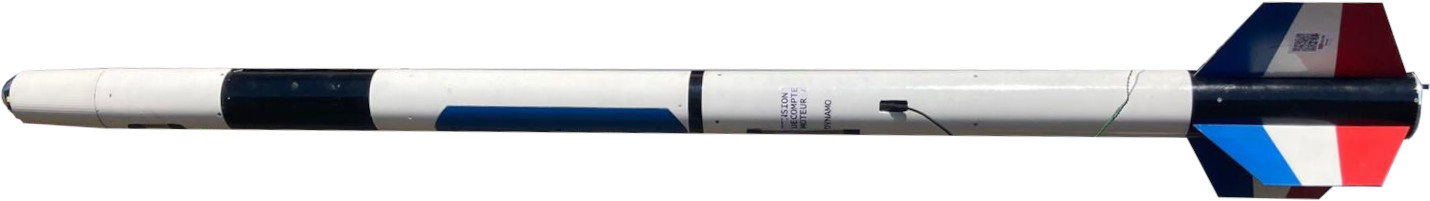
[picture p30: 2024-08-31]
Documentation/RapportDeProjet/img/Fusee.jpg

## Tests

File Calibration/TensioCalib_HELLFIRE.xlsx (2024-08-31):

Valeur brute | Masse
0 | 0
50 | 20
140 | 40
320 | 60
430 | 80
1023 | 120

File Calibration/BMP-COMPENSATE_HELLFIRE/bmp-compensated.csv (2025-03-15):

timestamp | UP | Pressure (Pa)
1382 | 40007 | 120968
1882 | 40008 | 120971
2382 | 40007 | 120968
2882 | 40007 | 120968
3382 | 40005 | 120962
3883 | 40006 | 120965
4382 | 40006 | 120965
4882 | 40007 | 120968
5382 | 40006 | 120965
5882 | 40006 | 120965
6382 | 40006 | 120965
6882 | 40005 | 120962
7382 | 40007 | 120968
7882 | 40007 | 120968
8382 | 40006 | 120965
8882 | 40007 | 120968
9382 | 40006 | 120965
9882 | 40007 | 120968
10382 | 40004 | 120958
10882 | 40005 | 120962
11382 | 40006 | 120965
11882 | 40003 | 120955
12382 | 40005 | 120962
12882 | 40004 | 120958
13382 | 40004 | 120958
13882 | 40005 | 120962
14382 | 40002 | 120952
14882 | 40004 | 120958
15382 | 40003 | 120955
15882 | 40006 | 120965
16382 | 40004 | 120958
16882 | 40006 | 120965
17382 | 40006 | 120965
17882 | 40004 | 120958
18382 | 40003 | 120955
18882 | 40003 | 120955
19382 | 40004 | 120958
19883 | 40004 | 120958
20382 | 40004 | 120958
20882 | 40004 | 120958
21382 | 40003 | 120955
21882 | 40002 | 120952
22382 | 40002 | 120952
22882 | 40002 | 120952
23382 | 40001 | 120950
23882 | 40002 | 120952
24382 | 40002 | 120952
24882 | 40002 | 120952
25382 | 40003 | 120955
25882 | 40000 | 120947
26382 | 40002 | 120952
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

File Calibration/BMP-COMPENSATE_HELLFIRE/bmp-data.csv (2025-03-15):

timestamp | UP
1382 | 40007
1882 | 40008
2382 | 40007
2882 | 40007
3382 | 40005
3883 | 40006
4382 | 40006
4882 | 40007
5382 | 40006
5882 | 40006
6382 | 40006
6882 | 40005
7382 | 40007
7882 | 40007
8382 | 40006
8882 | 40007
9382 | 40006
9882 | 40007
10382 | 40004
10882 | 40005
11382 | 40006
11882 | 40003
12382 | 40005
12882 | 40004
13382 | 40004
13882 | 40005
14382 | 40002
14882 | 40004
15382 | 40003
15882 | 40006
16382 | 40004
16882 | 40006
17382 | 40006
17882 | 40004
18382 | 40003
18882 | 40003
19382 | 40004
19883 | 40004
20382 | 40004
20882 | 40004
21382 | 40003
21882 | 40002
22382 | 40002
22882 | 40002
23382 | 40001
23882 | 40002
24382 | 40002
24882 | 40002
25382 | 40003
25882 | 40000
26382 | 40002
26882 | 40000
27382 | 40001
27882 | 40002
28382 | 40003
28882 | 40002
29382 | 40002
29882 | 40004
30382 | 40000
30882 | 40001
31382 | 40002
31882 | 40000
32382 | 40000
32882 | 40002
33382 | 39998
33882 | 40001
34382 | 40000
34882 | 40000
35382 | 39999
35883 | 40001
36382 | 40000
36882 | 40000
37382 | 40002
37882 | 40002
38382 | 39998
38882 | 40001
39382 | 40000
39882 | 40001
40382 | 39998
40882 | 40000
41382 | 39999
41882 | 40001
42382 | 40003
42882 | 39998
43382 | 40000
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

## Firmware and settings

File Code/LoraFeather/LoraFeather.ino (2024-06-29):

// M0 Lora Feather Code + LSM6DSOX sensor
// v0.1
// author : Mixcraftio

#define DEBUG True
#define GPSSerial Serial1 // HardwareSerial name GPS is connected to
#define PRINT(t)              \
  #if DEBUG == True           \
    Serial.print(t);          \
  #else                       \
    rf95.send(t, sizeof(t));  \
  #endif
#define PRINTLN(t)              \
  #if DEBUG == True           \
    Serial.println(t);          \
  #else                       \
    rf95.send(t, sizeof(t));  \
  #endif


#include <Adafruit_LSM6DSOX.h>
#include <Adafruit_GPS.h>

Adafruit_LSM6DSOX sox;
Adafruit_GPS GPS(&GPSSerial);

uint32_t time;
uint32_t previousTimeLSM = millis();
const uint16_t LSMInterval = 10;
uint32_t previousTimeGPS = millis();
const uint16_t GPSInterval = 1000;

void setup(void) {
  #if DEBUG == True
    Serial.begin(115200);
    PRINTLN("Initialising...");
    while (!Serial);
  #endif
  
  // Set ranges and init sensors
  GPS.begin(9600);
  GPS.sendCommand(PMTK_SET_NMEA_OUTPUT_RMCGGA);
  GPS.sendCommand(PMTK_SET_NMEA_UPDATE_1HZ);
  GPS.sendCommand(PGCMD_ANTENNA);
  delay(1000);
  GPS.println(PMTK_Q_RELEASE);
  sox.begin_I2C();
  sox.setAccelRange(LSM6DS_ACCEL_RANGE_16_G);
  sox.setGyroRange(LSM6DS_GYRO_RANGE_1000_DPS);
  sox.setAccelDataRate(LSM6DS_RATE_6_66K_HZ);
  sox.setGyroDataRate(LSM6DS_RATE_6_66K_HZ);

  #if DEBUG == True
    PRINTLN("Initialised!");
    printRates();
  #endif
}

#if DEBUG == True
  void printRates(){
    PRINT("Accelerometer range set to: ");
    switch (sox.getAccelRange()) {
      case LSM6DS_ACCEL_RANGE_2_G:
        PRINTLN("+-2G");
        break;
      case LSM6DS_ACCEL_RANGE_4_G:
        PRINTLN("+-4G");
        break;
      case LSM6DS_ACCEL_RANGE_8_G:
        PRINTLN("+-8G");
        break;
      case LSM6DS_ACCEL_RANGE_16_G:
        PRINTLN("+-16G");
        break;
    }

    PRINT("Gyro range set to: ");
    switch (sox.getGyroRange()) {
      case LSM6DS_GYRO_RANGE_125_DPS:
        PRINTLN("125 degrees/s");
        break;
      case LSM6DS_GYRO_RANGE_250_DPS:
        PRINTLN("250 degrees/s");
        break;
      case LSM6DS_GYRO_RANGE_500_DPS:
        PRINTLN("500 degrees/s");
        break;
      case LSM6DS_GYRO_RANGE_1000_DPS:
        PRINTLN("1000 degrees/s");
        break;
      case LSM6DS_GYRO_RANGE_2000_DPS:
        PRINTLN("2000 degrees/s");
        break;
      case ISM330DHCX_GYRO_RANGE_4000_DPS:
        break; // unsupported range for the DSOX
    }

    PRINT("Accelerometer data rate set to: ");
    switch (sox.getAccelDataRate()) {
      case LSM6DS_RATE_SHUTDOWN:
        PRINTLN("0 Hz");
        break;
      case LSM6DS_RATE_12_5_HZ:
        PRINTLN("12.5 Hz");
        break;
      case LSM6DS_RATE_26_HZ:
        PRINTLN("26 Hz");
        break;
      case LSM6DS_RATE_52_HZ:
        PRINTLN("52 Hz");
        break;
      case LSM6DS_RATE_104_HZ:
        PRINTLN("104 Hz");
        break;
      case LSM6DS_RATE_208_HZ:
        PRINTLN("208 Hz");
        break;
      case LSM6DS_RATE_416_HZ:
        PRINTLN("416 Hz");
        break;
      case LSM6DS_RATE_833_HZ:
        PRINTLN("833 Hz");
        break;
      case LSM6DS_RATE_1_66K_HZ:
        PRINTLN("1.66 KHz");
        break;
      case LSM6DS_RATE_3_33K_HZ:
        PRINTLN("3.33 KHz");
        break;
      case LSM6DS_RATE_6_66K_HZ:
        PRINTLN("6.66 KHz");
        break;
    }

    PRINT("Gyro data rate set to: ");
    switch (sox.getGyroDataRate()) {
      case LSM6DS_RATE_SHUTDOWN:
        PRINTLN("0 Hz");
        break;
      case LSM6DS_RATE_12_5_HZ:
        PRINTLN("12.5 Hz");
        break;
      case LSM6DS_RATE_26_HZ:
        PRINTLN("26 Hz");
        break;
      case LSM6DS_RATE_52_HZ:
        PRINTLN("52 Hz");
        break;
      case LSM6DS_RATE_104_HZ:
        PRINTLN("104 Hz");
        break;
      case LSM6DS_RATE_208_HZ:
        PRINTLN("208 Hz");
        break;
      case LSM6DS_RATE_416_HZ:
        PRINTLN("416 Hz");
        break;
      case LSM6DS_RATE_833_HZ:
        PRINTLN("833 Hz");
        break;
      case LSM6DS_RATE_1_66K_HZ:
        PRINTLN("1.66 KHz");
        break;
      case LSM6DS_RATE_3_33K_HZ:
        PRINTLN("3.33 KHz");
        break;
      case LSM6DS_RATE_6_66K_HZ:
        PRINTLN("6.66 KHz");
        break;
    }
    return;
  }
#endif

void loop() {
  // read data from the GPS in the 'main loop'
  char c = GPS.read();
  #if DEBUG == True
    if (c) PRINT(c);
  #endif
  // if a sentence is received, we can check the checksum, parse it...
  if (GPS.newNMEAreceived()) {
    // a tricky thing here is if we print the NMEA sentence, or data
    // we end up not listening and catching other sentences!
    // so be very wary if using OUTPUT_ALLDATA and trying to print out data
    // PRINT(GPS.lastNMEA()); // this also sets the newNMEAreceived() flag to false
    if (!GPS.parse(GPS.lastNMEA())) // this also sets the newNMEAreceived() flag to false
      return; // we can fail to parse a sentence in which case we should just wait for another
  }

  time = millis();
  if (time - previousTimeGPS >= GPSInterval) {
    // "GPS";arduinotime;fix;quality;time;date;locationlat;locationlng;speed;angle;altitude;satellites

    #if DEBUG == True
      PRINT("GPS;");
      PRINT(millis()); PRINT(";");
      PRINT((int)GPS.fix); PRINT(";");
      PRINT((int)GPS.fixquality);
      if (GPS.fix) {
        PRINT(";");
        if (GPS.hour < 10) { PRINT('0'); }
        PRINT(GPS.hour, DEC); PRINT(':');
        if (GPS.minute < 10) { PRINT('0'); }
        PRINT(GPS.minute, DEC); PRINT(':');
        if (GPS.seconds < 10) { PRINT('0'); }
        PRINT(GPS.seconds, DEC); PRINT('.');
        if (GPS.milliseconds < 10) {
          PRINT("00");
        } else if (GPS.milliseconds > 9 && GPS.milliseconds < 100) {
          PRINT("0");
        }
        PRINT(GPS.milliseconds);
        PRINT(";");
        PRINT(GPS.day, DEC); PRINT('/');
        PRINT(GPS.month, DEC); PRINT("/20");
        PRINT(GPS.year, DEC);
        PRINT(";");
        PRINT(GPS.latitudeDegrees, 10);
        // PRINT(GPS.lat); (N or S)
        PRINT(";");
        PRINT(GPS.longitudeDegrees, 10);
        // PRINT(GPS.lon); (W or E)
        PRINT(";");
        PRINT(GPS.speed);
        PRINT(";");
        PRINT(GPS.angle);
        PRINT(";");
        PRINT(GPS.altitude);
        PRINT(";");
        PRINT((int)GPS.satellites);
        PRINT(";");
        PRINT((int)GPS.antenna);
      }
      PRINT("\n");
    // #else
    #endif

    previousTimeGPS = millis();
  }

  time = millis();
  if (time - previousTimeLSM >= LSMInterval) {
    // "IMU";time;temp;ax;ay;az;gx;gy;gz

    sensors_event_t accel;
    sensors_event_t gyro;
    sensors_event_t temp;
    sox.getEvent(&accel, &gyro, &temp);

    #if DEBUG == True
    PRINT("IMU;");
    previousTimeLSM = millis();
    PRINT(millis()); PRINT(";"); // ms
    PRINT(temp.temperature); PRINT(";"); // °C

    PRINT(accel.acceleration.x); PRINT(";"); // m.s^-2
    PRINT(accel.acceleration.y); PRINT(";"); // m.s^-2
    PRINT(accel.acceleration.z); PRINT(";"); // m.s^-2

    PRINT(gyro.gyro.x); PRINT(";"); // rad.s^-1
    PRINT(gyro.gyro.y); PRINT(";"); // rad.s^-1
    PRINT(gyro.gyro.z); PRINT("\n"); // rad.s^-1
    // #else
    #endif

  }
}

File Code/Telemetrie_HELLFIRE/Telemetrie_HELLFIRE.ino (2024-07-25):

// Heltec Wireless Tracker + LSM6DSOX sensor
// v1.0
// author : Mixcraftio

// #include <SD.h>
#include <RadioLib.h>
#include <TinyGPSPlus.h>
// #include <Adafruit_LSM6DSOX.h>

// #define DEBUG
#ifdef DEBUG 
  #define PRINT(item) Serial.print(item)
#else
  #define PRINT(item) /*dataFile.print(item)*/
#endif

#define RADIO_DIO_1       14
#define RADIO_NSS         8
#define RADIO_RESET       12
#define RADIO_BUSY        13
#define SD_CHIP_SELECT    4
#define LSM_CHIP_SELECT   5
#define VGNSS_CTRL        3
#define DELAY_MESURE      20
#define FREQUENCY         869.138 //MHz
#define BANDWIDTH         125. //KHz
#define TX_POWER          20 //dBm

TinyGPSPlus GPS;
// Adafruit_LSM6DSOX sox;
// File dataFile;
SX1262 radio = new Module(RADIO_NSS, RADIO_DIO_1, RADIO_RESET, RADIO_BUSY);
// uint32_t timestamp;
// uint32_t prev_mes_timestamp = 0;
String dataString;
// String radioString;

void init_radio() {
  int state = radio.begin(FREQUENCY, BANDWIDTH, 9, 7, 18, TX_POWER);
  if (state != RADIOLIB_ERR_NONE) {
    PRINT("Lora init failed with error code : ");
    PRINT(state); PRINT("\n");
    delay(1000);
    init_radio();
  }
}

// void init_SD() {
//   if(!SD.begin(SD_CHIP_SELECT)) {
//     PRINT("Card Mount Failed\n");
//     delay(1000);
//     init_SD();
//   }
// }

// void init_File() {
//   dataFile = SD.open("/DATA.TXT", FILE_WRITE);
//   if(!dataFile) {
//     PRINT("Opening file failed\n");
//     delay(1000);
//     init_File();
//   }
// }

void init_GNSS() {
  pinMode(VGNSS_CTRL,OUTPUT);
  digitalWrite(VGNSS_CTRL,HIGH);
  Serial1.begin(115200,SERIAL_8N1,33,34);    
  while(!Serial1);
}

// void init_IMU() {
//   if (!sox.begin_SPI(LSM_CHIP_SELECT)) {
//     PRINT("LSM6DSOX init failed\n");
//     delay(1000);
//     init_IMU();
//   }
// }

void setup(void) {
  pinMode(18,OUTPUT);
  digitalWrite(18,HIGH);
  #ifdef DEBUG
    Serial.begin(115200);
    while (!Serial) delay(10);
  #endif

  init_radio();
  // init_SD();
  // init_File();
  init_GNSS();
  String mes="FX10;Connected\n";
  radio.transmit(mes);
  // init_IMU();
  // sox.setAccelRange(LSM6DS_ACCEL_RANGE_16_G);
  // sox.setGyroRange(LSM6DS_GYRO_RANGE_1000_DPS);
  // sox.setAccelDataRate(LSM6DS_RATE_208_HZ);
  // sox.setGyroDataRate(LSM6DS_RATE_208_HZ);

  #ifdef DEBUG
    Serial.println("Setup done!");
  #endif
  // prev_mes_timestamp = millis();
}

void loop() {
  // timestamp = millis();
  // if ((timestamp - prev_mes_timestamp) >= DELAY_MESURE) {
  //   // "FX10";"IMU";time;temp;ax;ay;az;gx;gy;gz
  //   sensors_event_t accel;
  //   sensors_event_t gyro;
  //   sensors_event_t temp;
  //   sox.getEvent(&accel, &gyro, &temp);

  //   PRINT("FX10;IMU;");
  //   PRINT(temp.temperature); PRINT(";");
  //   PRINT(accel.acceleration.x); PRINT(";");
  //   PRINT(accel.acceleration.y); PRINT(";");
  //   PRINT(accel.acceleration.z); PRINT(";");
  //   PRINT(gyro.gyro.x); PRINT(";");
  //   PRINT(gyro.gyro.y); PRINT(";");
  //   PRINT(gyro.gyro.z);
  //   PRINT("\n");

    // radioString = "IMU;"+String(temp.temperature)+";"+
    //               String(accel.acceleration.x)+";"+
    //               String(accel.acceleration.y)+";"+
    //               String(accel.acceleration.z)+";"+
    //               String(gyro.gyro.x)+";"+
    //               String(gyro.gyro.y)+";"+
    //               String(gyro.gyro.z)+"\n";
    // radio.transmit(radioString);

  //   prev_mes_timestamp += DELAY_MESURE;
  // }
  
  if(Serial1.available()>0) {
    // "FX10";"GPS";fix;quality;time;date;locationlat;locationlng;speed;angle;altitude;satellites
    if(Serial1.peek()!='\n') {
      GPS.encode(Serial1.read());
    } else {
      Serial1.read();
      if(GPS.location.isUpdated()) {
        dataString = "FX10;GPS;;;"+String(GPS.time.hour())+":"+String(GPS.time.minute())+":"+String(GPS.time.second())+";;"+String(GPS.location.lat(),5)+";"+String(GPS.location.lng(),5)+"\n";
        PRINT(dataString);
        radio.transmit(dataString);
        // #ifndef DEBUG
        //   dataFile.flush();
        // #endif
      }
    }
	}
}

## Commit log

2024-01-27 Kicad modifications + components list update
    [Hellfire.kicad_pcb, Hellfire.kicad_pcb_bom.csv, Hellfire.kicad_pcb_positions.csv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]
2024-02-03 Hellfire+pcb update
    [Hellfire.kicad_pcb]
2024-04-28 remove Minuterie PCB (to Nextcloud archive)
    [Hellfire.kicad_pcb, Hellfire.kicad_pcb_bom.csv, Hellfire.kicad_pcb_positions.csv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]
2024-04-28 Add boards-related instructions
2024-04-28 Update StabTraj
    [ST-(StabTraj)_HELLFIRE.xlsx]
2024-06-29 Update code
    [M0Logger+LSM6DSOX.fzz, ST-(StabTraj)_HELLFIRE.xlsx]
2024-07-05 Update code and add Fritzing files
    [M0Logger+LSM6DSOX.fzz, RX-WirelessTracker.fzz, TX-WirelessTracker-Apart.fzz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]
2024-07-09 Code updates
    [RX-WirelessTracker.fzz, TX-WirelessTracker-Apart.fzz, TX-WirelessTracker.fzz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]
2024-07-25 Analyse 1
    [ST-(StabTraj)_HELLFIRE.xlsx, TensioCalib_HELLFIRE.xlsx]
2024-08-31 Analyse 2
    [TensioCalib_HELLFIRE.xlsx]
2024-11-05 Update graphs - results exploitation - calibration
2024-11-09 Add sensor documentation
2025-03-15 Add BMP compensation calculations
    [bmp-compensated.csv, bmp-data.csv]
2025-03-15 IMU 3 val moy
2025-05-25 Traduction des comentaires
